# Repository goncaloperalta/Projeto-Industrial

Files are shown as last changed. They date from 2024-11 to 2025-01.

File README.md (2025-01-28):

# Automatic, universal push-button actuator, equipped with force gauge
## Table of contents
- [Overview](#overview)
- [Requirements](#requirements)
- [Pre-installation](#pre-installation)
- [Installation](#installation)
- [Interacting with the system](#interacting-with-the-system)

## Overview
This repository contains all the code to run the system, the PCB's files and the 3D designs.

## Requirements
This software is expected to run on a Raspberry Pi 4B (or equivalent), running **Raspberry Pi OS** not needing the graphical interface. 

## Pre-installation
Before installing, you must configure the way you want to connect to the Raspberry.
You can either connect it to the local network or use it has an access point.
> The former option is worse since you may run into conflits if the gateway ip of the local network and the ip of the DUT are the same.

To enable the access point run the command:

	sudo nmcli device wifi hotspot ssid <network-name> password <password>

If you want to disable it:

	sudo nmcli device disconnect wlan0
	sudo nmcli device up wlan0

The ethernet port must also be configured to have a static IPv4 (something like `192.168.1.5`), the gateway IP must be `192.168.1.1` and the route should not be set as default. That can be done using the `nmtui` command:

	sudo nmtui

You **must** also create a file inside the [control-code](control-code/) folder called `credentials.py`. The contents of the file should be the credentials used to connect to the DUT via SSH, formatted as:

	host="<hostname of the DUT>"
	pass="<password>"

without the characters `<` and `>`. 
## Installation
Start by installing `docker` and `docker-compose` with:

	sudo apt install docker.io docker-compose

then add your user to docker:

	sudo gpasswd -a $USER docker
	newgrp docker

finally clone the repository, `cd` into it and run a container with:

	docker compose up -d --build

Since this is the first time, it may take some minutes to finish building. After that you should see on port `:3000` the home page of the interface running, meaning the system is ready.

## Interacting with the system
The main way to interact with the system is to use the web interface on port `:3000`, however you can also use the a RESTful API on port `:8000`. On the **API Reference** page of the web interface you can see all the endpoints, what the returns are and a sample code to use it, you can also view the [api-reference.pdf](documents/api-reference.pdf) file which contains the same content.

The API is independent of the web interface and can be run without it but the opposite is not possible.

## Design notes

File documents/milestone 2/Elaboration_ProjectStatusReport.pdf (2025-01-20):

## 42088 – Industrial Project

# Project Status Report

## Milestone 2 – Elaboration

Project name: | Automatic, universal push-button actuator, equipped with force gauge
Customer: | Altice Labs
Customer supervisor: | Eng. Hélder Alves Eng. Nuno Balseiro
Date issued: | 06/11/2024
Team members: | Coordinator: Cláudia Almeida, claudiasalmeida@ua.pt, 914102617. Other team members: Rafael Alves, rafael01@ua.pt , 937353627. Gonçalo Peralta, goncaloperalta@ua.pt , 916828627. Pedro Matias, pedrodsmatias@ua.pt , 917126548.
Supervisor: | Professor Pedro Fonseca
Class supervisor: | Professor Pedro Fonseca

## Management summary:

The project is on track to meet its delivery deadlines. The team has successfully finished the Inception phase and is now actively working on the Elaboration phase. The component list, hardware circuit designs, and use case definitions are all now being finalized. There have been no substantial delays, and all the important components are being scheduled for purchasing within the current timeframe. As a consequence of the most recent meetings with the customer and the project supervisor, where the more technical issues were discussed, the electronic components were picked to ensure the product's flawless operation, resulting in an adjustment to the final budget. As we move into the Construction phase, the integration of the actuator, force sensor, and API, with iterative testing will be closely monitored, intended to address any compatibility issues early on.

## Architecture

The architecture of the system consists of three main components: the Control Unit, the Control Electric Circuit, and the Mechanical Actuation.

- The Control unit is managed by a Raspberry Pi that runs the control software and serves as the central processing component for the system. The Raspberry Pi generates a PWM (Pulse

Width Modulation) signal to regulate the actuator’s movement, allowing for controlled button pressing with variable force. It also maintains a Secure Shell (SSH) connection with the DUT, allowing it to detect feedback from the device in real time, such as system responses or status changes upon a button click. For force measurement, the Raspberry Pi reads data from the force sensor using I2C/SPI protocols, ensuring accurate and timely data transfer from the sensor to the control software.

- The Control electric circuit amplifies the PWM signal generated by the Raspberry Pi, ensuring sufficient power is supplied to the actuator. This circuit includes an H-Bridge, allowing current to flow in both directions as required to control the actuator’s movement accurately. The circuit, powered by a 12V, 3A DC power source, will provide the energy needed to drive the actuator with stability and precision, allowing for both pressing and releasing movements, required for testing various types of buttons.
- The Mechanical Actuation assembly is designed to interface directly with the DUT, positioning the actuator over the buttons to be tested. This component includes a clamp that securely attaches to the DUT, providing flexibility and adaptability for different button placements and device sizes. Mounted within the clamp is a linear actuator that performs the physical pressing of the buttons, with a force sensor placed behind the actuator to capture the exact force applied during each press. This assembly connects to a PCB board, which relays signals from the force sensor back to the Control Unit, ensuring accurate control and data capture throughout the testing process.

Figure 1 shows the improved and updated mechanical design of the product.

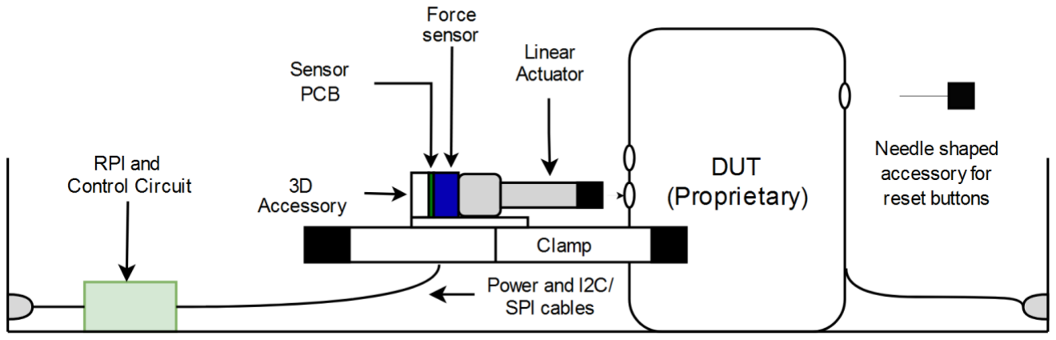
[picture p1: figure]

Figure 1. Mechanical assembly of the product.

Figure 2 shows the Unified Modelling Language (UML) Sequence Diagram, which represents the interaction amongst the different components of the system.

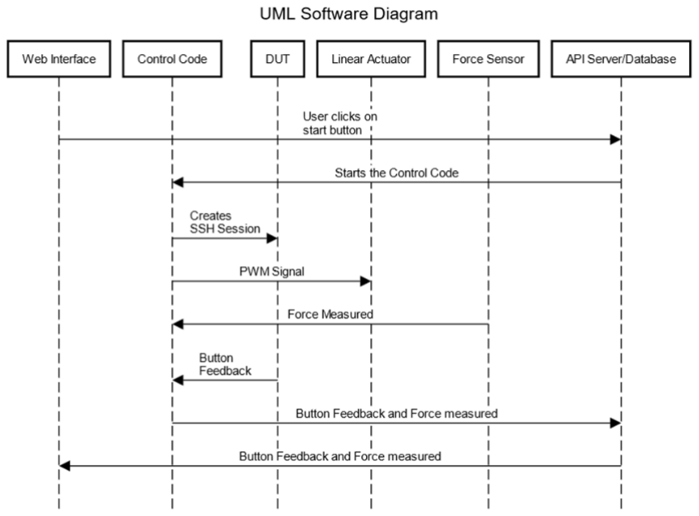
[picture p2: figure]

Figure 2. UML Diagram.

## Key milestones

ID | Description | Original planned completion date | Current planned completion date | Actual completion date
Project Vision | Market and needs to which the project responds | 23/10/2024 | --- | 23/10/2024
Project Plan | Working Phases, Budget and Risk List | 23/10/2024 | --- | 23/10/2024
Mock Up | A physical model of the system | 23/10/2024 | --- | 23/10/2024
Hardware | Final Component Lists | 30/10/2024 | 5/11/2024 | 6/11/2024
Project Status Report – M2 Elaboration | A summary of the current project status | 6/11/2024 | 6/11/2024 | 6/11/2024

Project Use
Cases – M2
Elaboration

Description of user interaction with
the product | 6/11/2024 | 6/11/2024 | 6/11/2024
Software Web Interface | Suggested visual presentation of the web interface | 13/11/2024 | 13/11/2024
Hardware PCB’s design | Design of the system's printed circuits and electrical circuits | 13/11/2024 | 20/11/2024

## Progress and deviation from plan

The project has generally progressed well; however, finalizing and structuring the component list took an additional seven days beyond the original timeline. This delay has impacted the timeline for requesting and purchasing the components, which may cause slight setbacks in the hardware assembly phase. To overcome this impediment of progress on the hardware testing side, we're going to move forward with the printed circuit boards, which are a fundamental part of starting tests, and start working and simulating data reception on the Raspberry Pi's web interface.

## Work plan for next iteration

In the next iteration, our primary focus will be on the design of the hardware printed circuit boards (PCBs) to support the control electric circuit for the actuator and force sensor. As the team anticipates some waiting time for component deliveries, we plan to adjust our schedule by beginning web page development for the Raspberry Pi ahead of schedule and design some visual presentation of the Web interface itself in various stage of its use. This will allow us to lay the foundation for the control interface, enabling future integration with the actuator and force sensor. Table 2 shows the sprint plan updated.

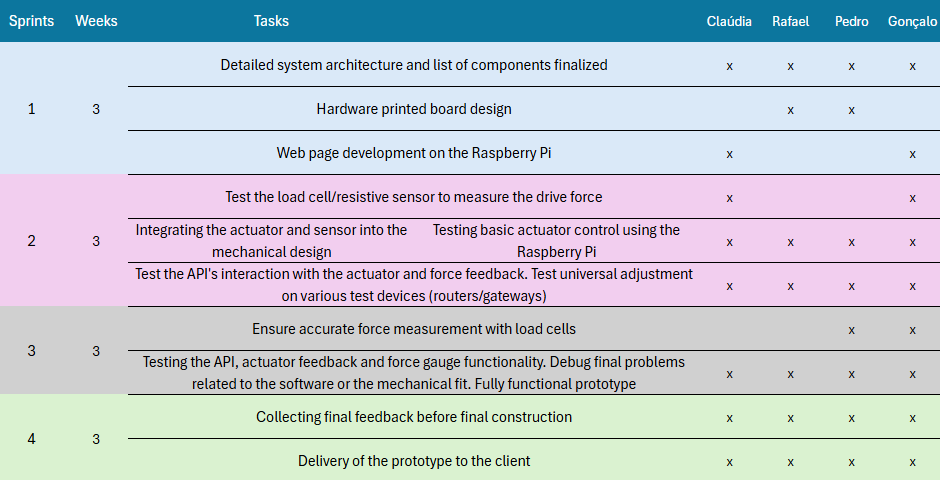
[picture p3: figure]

Table 2. Work sprints plan and schedule.

## Financial status

Following the development of the system's architecture in the previous iteration report, the team undertook a more in-depth investigation of the components needed to achieve the project specifications. This extensive analysis proved that our initial component selections were generally correct. However, it resulted in a significant rise in the overall budget.
One of the main factors contributing to this rise is the necessity for components with operating ranges and characteristics that better match our project's requirements, which are much more expensive. For instance, we wanted to replace the linear actuator to a type with a lower maximum force to ensure compatibility with our system, but this model costs roughly triple the amount. Similarly, we chose a more precise force sensor because force measurement is crucial for our product. This sensor, while more expensive, will significantly improve the accuracy and reliability of test results.
The remaining increase in the overall cost is due to small and inexpensive components that we did not include in the previous presented budget.

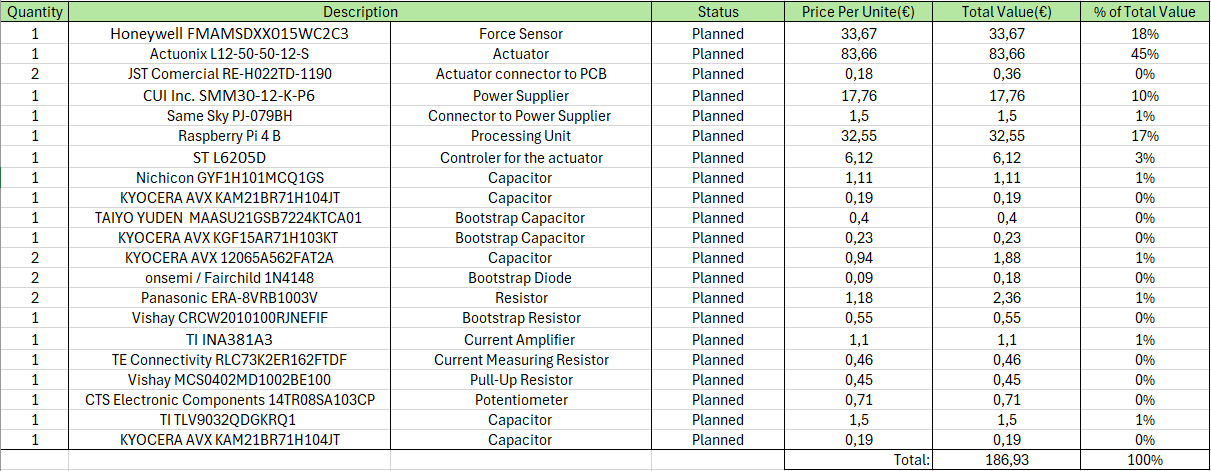
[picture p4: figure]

## Group contribution

Group member | Major contributions | Work share (%)
Cláudia Almeida | Team coordinator, responsible for organizing regrouping sessions and managing communication with external parties. Primary editor of written documents, developed the use cases, studied market relevance for industrial automation, and led Milestone 1 presentation. | 25
Rafael Alves | Developed the final hardware components list, analysed project risks for each phase and proposed mitigation strategies, and led Milestone 1 presentation. | 25
Gonçalo Peralta | Created all system diagrams and drafts of the mechanical product for documentation, developed the block diagrams and use cases, sprints spread calendar and led the initial planning for the software approach to the project. | 25
Pedro Matias | Contributed to researching and finalizing the hardware components list and supported the assessment of technical needs for project phases. | 25

## Comments and remarks

Attached are the documents relating to the risk analysis of the project and the block diagrams of the system broken down into various levels.

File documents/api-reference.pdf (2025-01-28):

# API Reference

This web interface runs on port :3000 , however the system also provides a RESTful API on port :8000 . Anything done in this web interface is based on this API.
The API accepts and returns only JSON encoded objects with no need for authentication. There are diferent ways to use it, one is with Python :

import requests
url = 'http://<ip>:8000/<Endpoint>'
headers = {
"Content-type": "application/json" }

res = requests.get(url, headers=headers)
print(res.text)

In each of the endpoints bellow it's provided the expected returns and a sample code to use it. All code can be seen on the GitHub (https://github.com/goncaloperalta/Projeto-Industrial) repository.

STATUS

GET | /api | ⮝

Returns a message if the API is up and running.

{
"message": "API running."
}

Sample python code:

import requests

url = "http://localhost:8000/api" headers = {
"Content-type": "application/json" }
res = requests.get(url, headers=headers)
print(res.text)
GET | /get-status | ⮝

Returns a message with the current state which can be on of the following:

{
// Ready to start a test
"message": "Ready"
// Already running a test
"message": "Running a test" // Aborting the running test "message": "Aborting the test" }

Sample python code:

import requests

url = "http://localhost:8000/get-status" headers = {
"Content-type": "application/json" }
res = requests.get(url, headers=headers)
print(res.text)
GET | /get-current-parameters | ⮝

If a test is running, returns an object with the parameters being used:

{ // If a test is running
"pressTime": 0
"pressTime": 1
"pressTime": 0
}
{ // If no test is running "message": "Not running a test" }

Sample python code:

import requests

url = "http://localhost:8000/get-current-parameters" headers = {
"Content-type": "application/json"
}
res = requests.get(url, headers=headers)
print(res.text)
GET | /get-logs | ⮝

Returns a file with the logs of the last test done. Can be accessed by just opening on the browser.

RUN A TEST

POST | /start | ⮝

Starts a button test, with the given parameters or profile chosen. If a valid profile is given the other parameters are ignored. A request with no body starts the test with parameter nTimes equal to one an the others set to zero. Returns one of the following messages:

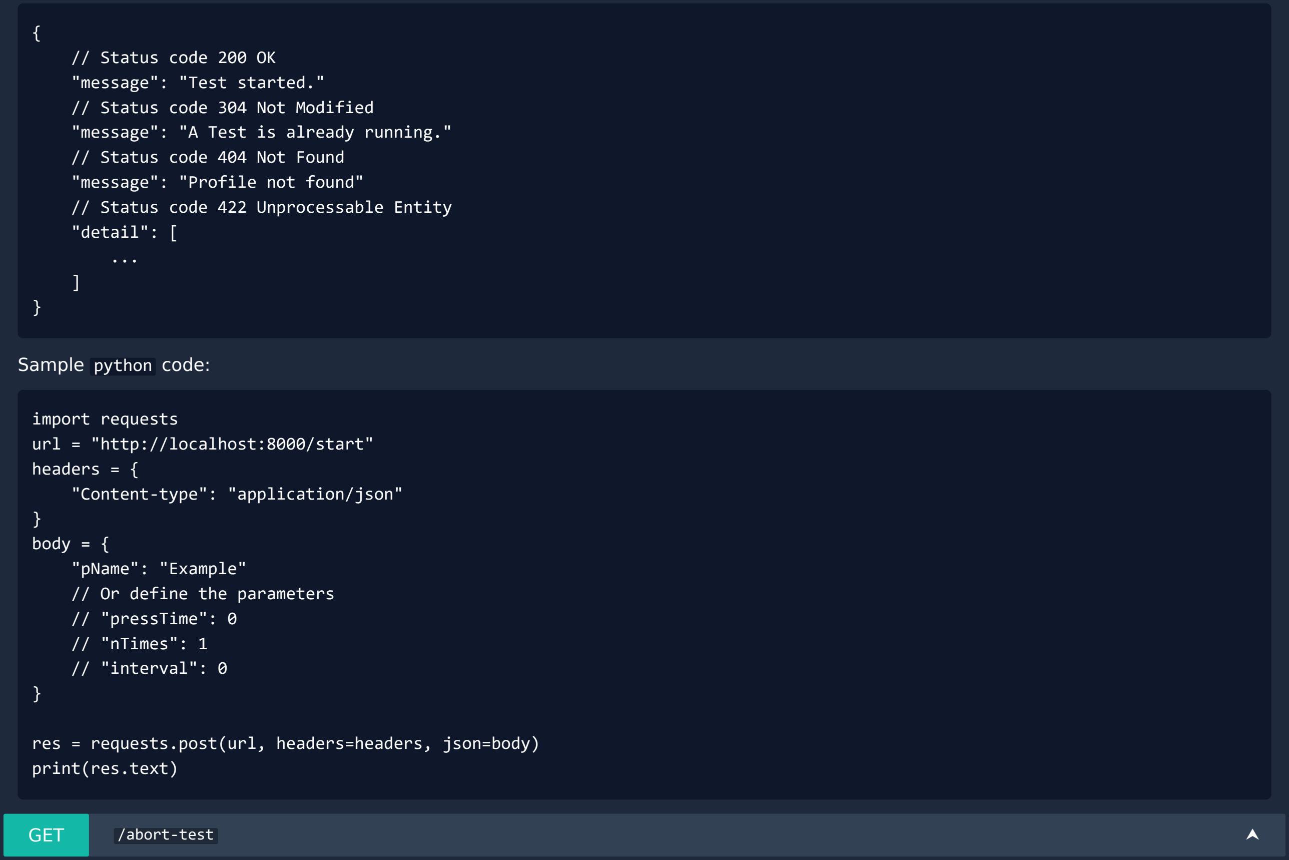
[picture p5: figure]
// Status code 200 OK "message": "Test started." // Status code 304 Not Modified "message": "A Test is already running." // Status code 404 Not Found "message": "Profile not found" // Status code 422 Unprocessable Entity "detail": [ ...; Sample python code:; import requests url = "http://localhost:8000/start" headers = { "Content-type": "application/json"; } body = { "pName": "Example" // Or define the parameters // "pressTime": 0 // "nTimes": 1 // "interval": 0; res = requests.post(url, headers=headers, json=body) print(res.text); GET; /abort-test

If a test is running aborts it. The test will only abort after finishing the current actuation

{
"message": "No test to abort" "message": "Test Aborted"
}

Sample python code:

import requests

url = "http://localhost:8000/abort-test" headers = {
"Content-type": "application/json" }
res = requests.get(url, headers=headers) print(res.text)

TESTS DATA

GET | /get-test-data | ⮝

Returns a file a JSON file with the all tests done from newest to oldest. Using a browser you can open the link directly and a download should appear. Data has the format:

[
{
"id": 5,
"button": "WPS",
"success": 1,
"error": "No error",
"presses": 2,
"parameters": "[0, 2, 1]",
"force_val": "[[1, 2, 3, 4, 5], [1, 2, 3, 4, 5]]", "time_val": "[[1, 2, 3, 4, 5], [1, 2, 3, 4, 5]]", "date": "2024-12-30",
"time": "11:45:43"
},
]
GET | /get-tests | ⮝

Returns all tests done, from newest to oldest, with format:

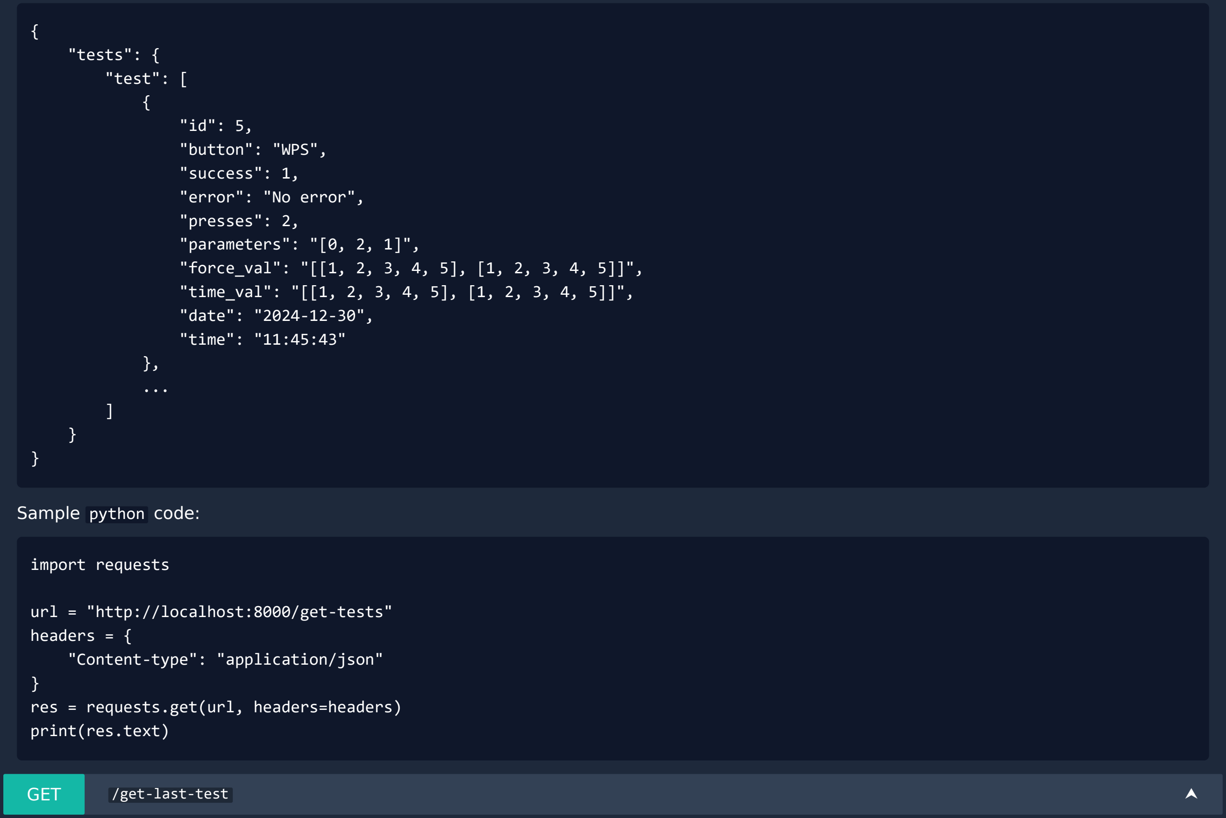
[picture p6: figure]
"tests": { "test": [ {; "id": 5, "button": "WPS", "success": 1, "error": "No error", "presses": 2, "parameters": "[0, 2, 1]",; "date": "2024-12-30", "time": "11:45:43"; Sample python code:; import requests; url = "http://localhost:8000/get-tests" headers = { "Content-type": "application/json"; } res = requests.get(url, headers=headers) print(res.text); GET; /get-last-test

"force_val": "[[1, 2, 3, 4, 5], [1, 2, 3, 4, 5]]", "time_val": "[[1, 2, 3, 4, 5], [1, 2, 3, 4, 5]]",

Returns only the last test done:

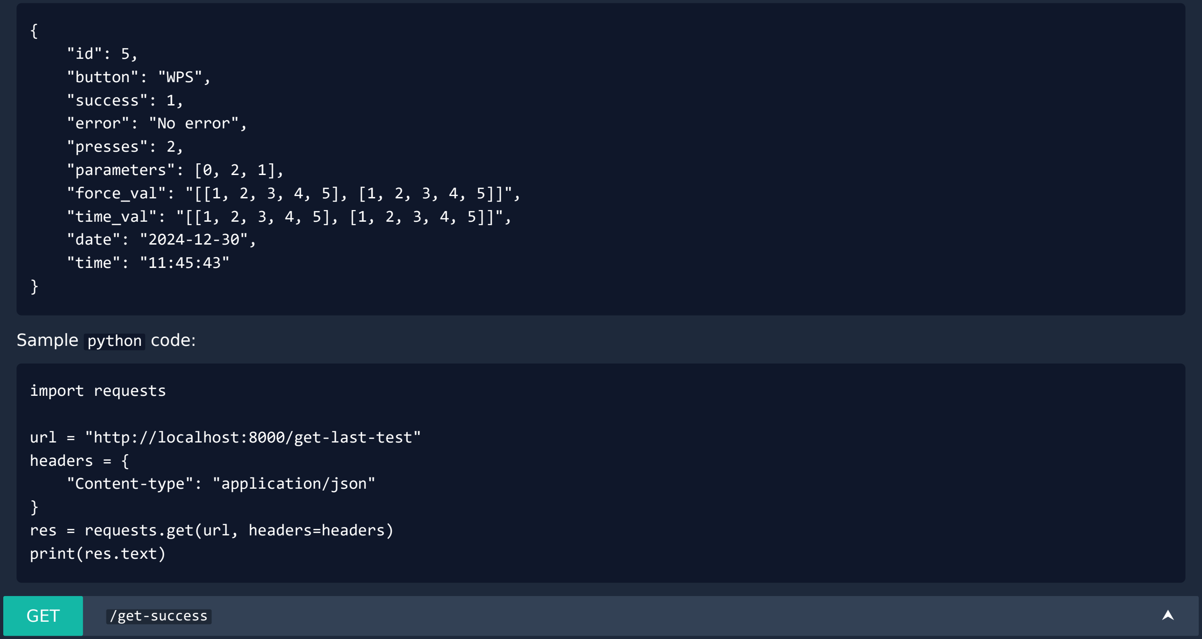
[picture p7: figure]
"id": 5, "button": "WPS", "success": 1, "error": "No error", "presses": 2, "parameters": [0, 2, 1],; "date": "2024-12-30", "time": "11:45:43"; Sample python code:; import requests; url = "http://localhost:8000/get-last-test" headers = { "Content-type": "application/json"; } res = requests.get(url, headers=headers) print(res.text); GET; /get-success

"force_val": "[[1, 2, 3, 4, 5], [1, 2, 3, 4, 5]]", "time_val": "[[1, 2, 3, 4, 5], [1, 2, 3, 4, 5]]",

Returns the success of all tests done:

[
1,
1,
0,
]

Sample python code:

import requests

url = "http://localhost:8000/get-success" headers = {
"Content-type": "application/json"
}
res = requests.get(url, headers=headers)
print(res.text)
POST | /get-tests-range | ⮝

Returns a defined range of tests:

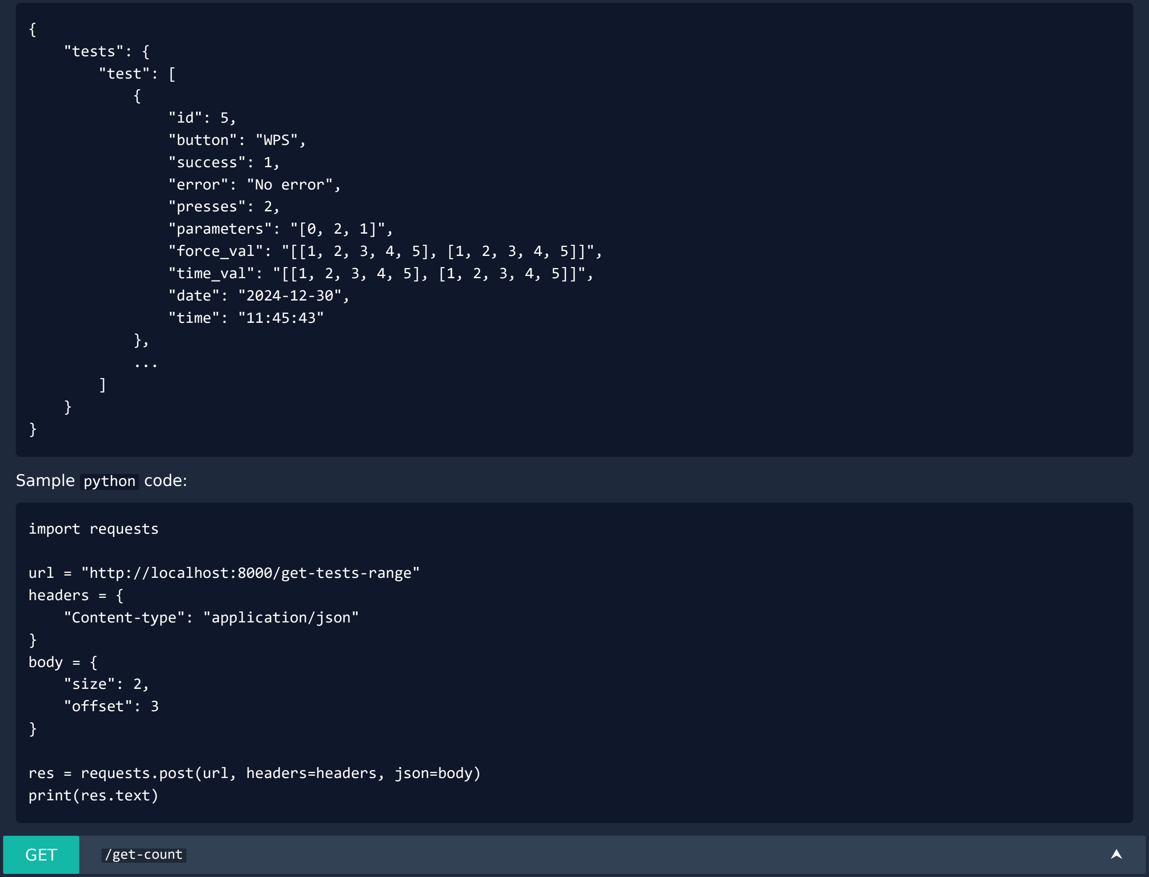
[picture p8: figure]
"tests": { "test": [ {; "id": 5, "button": "WPS", "success": 1, "error": "No error", "presses": 2, "parameters": "[0, 2, 1]",; "date": "2024-12-30", "time": "11:45:43"; Sample python code:; import requests; url = "http://localhost:8000/get-tests-range" headers = { "Content-type": "application/json"; } body = { "size": 2, "offset": 3; res = requests.post(url, headers=headers, json=body) print(res.text); GET; /get-count

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

Returns the total number of tests done:

{
"count": 19
}

Sample python code:

import requests

url = "http://localhost:8000/get-count" headers = {
"Content-type": "application/json" }
res = requests.get(url, headers=headers)
print(res.text)
POST | /get-by-id | ⮝

Returns the test data with the same id:

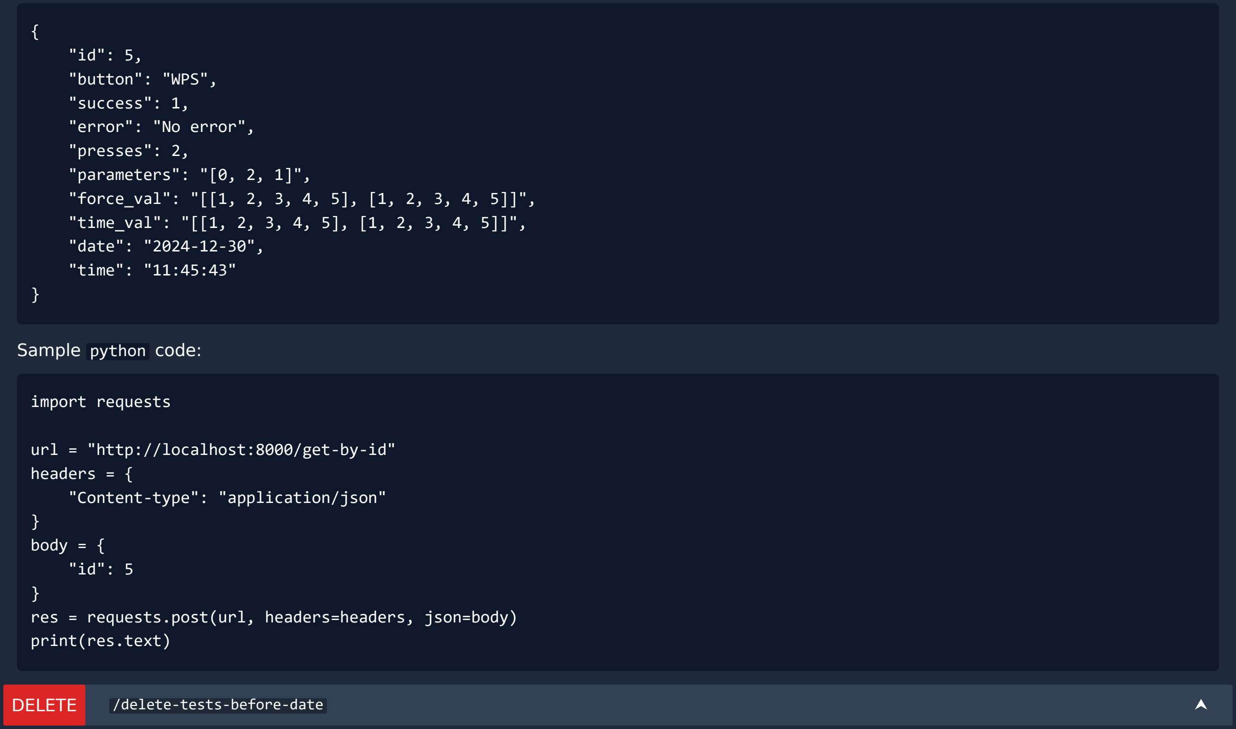
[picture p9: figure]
"id": 5, "button": "WPS", "success": 1, "error": "No error", "presses": 2, "parameters": "[0, 2, 1]",; "date": "2024-12-30", "time": "11:45:43"; Sample python code:; import requests; url = "http://localhost:8000/get-by-id" headers = { "Content-type": "application/json"; } body = { "id": 5; } res = requests.post(url, headers=headers, json=body) print(res.text); DELETE; /delete-tests-before-date

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

Deletes all tests before the given date:

{
"message": "Tests deleted" }

Sample python code:

import requests

url = "http://localhost:8000/delete-tests-before-date" headers = {
"Content-type": "application/json"
}
body = {
"day": "2024-12-30"
}
res = requests.delete(url, headers=headers, json=body) print(res.text)

PROFILES

GET | /get-profiles | ⮝

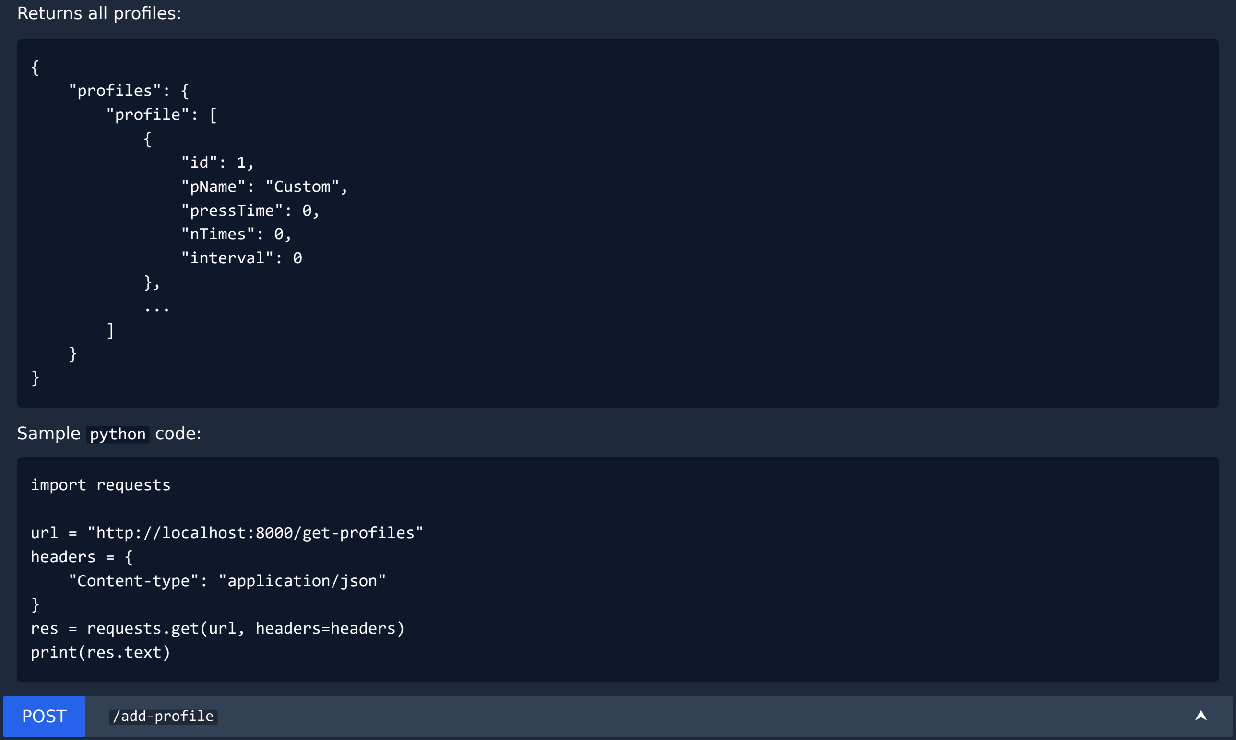
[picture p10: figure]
Returns all profiles:; "profiles": { "profile": [ {; "id": 1, "pName": "Custom", "pressTime": 0, "nTimes": 0, "interval": 0; Sample python code:; import requests; url = "http://localhost:8000/get-profiles" headers = { "Content-type": "application/json"; } res = requests.get(url, headers=headers) print(res.text); POST; /add-profile

Add a new profile with given parameters and name. Returns one of the messages:

{
"message": "Profile added to database." | // Status code 201 Created
"message": "A profile with that name already exists." | // Status code 400 Bad Request
}

Sample python code:

import requests

url = "http://localhost:8000/add-profile" headers = {
"Content-type": "application/json"
}
body = {
"pName": "Test Profile",
"pressTime": 3,
"nTimes": 2,
"interval": 1
}

res = requests.post(url, headers=headers, json=body)
print(res.text)
DELETE | /delete-profile | ⮝

Deletes a profile given it's name. Returns on of the messages:

{
"message": "Profile deleted from database." | // Status code 200 OK
"message": "Profile name not found." | // Status code 404 Not Found
}

Sample python code:

import requests

url = "http://localhost:8000/delete-profile" headers = {
"Content-type": "application/json"
}
body = {
"pName": "Test Profile"
}

res = requests.delete(url, headers=headers, json=body) print(res.text)

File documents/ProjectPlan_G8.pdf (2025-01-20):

## 42088 – Industrial Project

# Project Plan

Project name: | Automatic, universal push-button actuator, equipped with force gauge
Customer: | Altice Labs
Team members: | Coordinator: Cláudia Almeida, claudiasalmeida@ua.pt, 914102617. Other team members: Gonçalo Peralta, goncaloperalta@ua.pt , 916828627. Pedro Matias, pedrodsmatias@ua.pt , 917126548.

Rafael Alves, rafael01@ua.pt , 937353627.

Date: | 22/10/2024

Revision History
Date | Issue | Description | Author
22/10/2024 | Development Costs | Task phasing | Eng. Hélder Alves

## Objectives

The purpose of this project is to create a remotely controllable automaton that is capable of pressing buttons, validate their operation, measure the force required to activate them and communicate the results to the server. The solution must ensure that it interacts with various types of buttons (from soft-touch buttons to hard mechanical ones) safely and reliably, while collecting detailed data on the force applied and the button's response.
To achieve the intended end-result, an estimate of the required work was sub-divided into phases. This allows for efficient use of the group’s efforts to deliver an end-product with good characteristics and within the defined time frame.
Therefore, this report´s primary goal isto give a thorough assessment of how the work will be divided, how the project management will be done, the resources available for its development and the risks involved.

## Phase plan

Table 1. Work plan and schedule.

## 1.1 Objectives of each iteration

As seen in table 1, the project’s life cycle was divided into 4 major phases that in turn are divided into iterations. These divisions were pre-defined by the course with basis on an OpenUP framework, with a presentation on the end of each (and in the middle of the “Construction”) phase to show all progress achieved.

Inception
This report is written in the end of the Inception phase, and its main objective was to ensure that the entire group had a clear understanding of the proposed work, and the steps required to successfully complete it. More specifically, it was necessary to understand the purpose of the product and the needs
Week | Date
1 | 18/09/2024
2 | 25/09/2024

3

Meeting and Brainstorm with the Company

Team approval of project
requirements and initial design concepts
| 17/10/2024
4 | 23/10/2024
5 | 30/10/2024
6 | 11/06/2024
7 | 13/11/2024
8 | 20/11/2024

9

Integrating the actuator and sensor into
the mechanical design

Testing basic actuator control using the Raspberry Pi

| 27/11/2024
10 | 12/04/2024
12 | 25/12/2024
13 | 01/01/2025

15
16
17 | 17/1/2025

Web page development on the Raspberry Pi

Construction

Test the load cell/resistive sensor to measure the drive force

Transition

Delivery of the prototype to the client

Test the API's interaction with the actuator and force feedback. Test universal adjustment on various test devices (routers/gateways)

Ensure accurate force measurement with load cells

Inception

Detailed system architecture and list of components finalized

Hardware printed board design

Task
Understand the problem, determine initial requirements and submit proposals with solutions

Definition of the concept to be developed in the project

Elaboration

11 | 12/11/2024

Collecting final feedback before final construction

Testing the API, actuator feedback and force gauge functionality. Debug final
problems related to the software or the mechanical fit. Fully functional prototype

01/08/2025 of the devices under test (DUT), in order to create a timeline, a project and team management plan, and to develop a list of necessary components along with the corresponding budget, as well as a list of potential associated risks, ensuring an appropriate response to the problem presented.

Elaboration
In this phase the main objective is to define the system architecture and to transform the high-level vision developed during the Inception Phase into a practical and concrete plan for building the system. This means the system’s architecture will be clearly defined, including its structure, components and how they interrelate. This architecture will serve as the blueprint for development, providing a detailed plan of how the system will be built, operated and maintained. This phase focuses on organising the various parts of the system (e.g., actuator, force sensor, Raspberry Pi, API and software interface) in a way that illustrates how they will interact. By defining these interrelationships early, the team can ensure that all components work together seamlessly, and potential integration issues are addressed upfront. Here, proof of concepts and prototypes will play a significant role in mitigating risks. By testing core components (such as the actuator's control and the force sensor’s accuracy), potential issues can be identified early, and solutions can be refined before full-scale construction begins.
We will also take a deeper plunge into drawing up the necessary technical specifications for each component. This includes selecting the most suitable technologies (e.g. linear actuators, resistive force sensors), outlining the printed circuit board (PCB), defining the data flow and specifying the signal conditioning circuits and other essential infrastructures.
Since the goal is to take the general vision from Inception and break it down into detailed, actionable plans, technical diagrams, flowcharts, and interface definitions will be created to explain "how" the system will be implemented—whether it’s the physical setup of the actuator, the software architecture for the API, or the integration of the force sensor and data transmission protocols.

Construction
The goal of this phase is to start building the product that was designed in the earlier stages. Having the components required in hand, work force is focused on constructing the modules and testing them. The effort required to complete this task is likely high, and as such requires parallelism, minimizing stalls and delivery times.

For this, the development is split into two concurrent development trees, the API and the hardware. Both start with lower-level component development and testing to guarantee a solid foundation - for example the force sensor, and the base operating system for the Raspberry Pi - and rise to the model expected – e.g. proper motor control and working API.
The evolution of each tree will not be done top-down simply in one version, but rather it will be done in iterations that allow the communication between the API and the mechanical interface to be achieved as quickly as possible so to increment functionality. Afterwards, they will be fully tested in conjunction to achieve a working product.

Transition
In this phase, the final product will be delivered and presented, and so it should be a fully functioning product to be tested by users. From there feedback will be used to improve the experience and ensure it works as intended. We will conduct an evaluation of the satisfaction level from our side, as well as from the company and the professors.

## 2 Budget

This is a raw estimate of the cost associated with this product, but it will be more accurately updated in the elaboration phase.

ID | Category | Description | Value (€)
1 | Components | Linear Actuator https://mauser.pt/catalog/product_info.php?products_id=0 95-0732 (https://mauser.pt/catalog/product_info.php?products_id=095-0732) | 32.65
2 | Components | Raspberry Pi https://mauser.pt/catalog/product_info.php?products_id=0 95-3807 (https://mauser.pt/catalog/product_info.php?products_id=095-3807) | 19.99
3 | Components | Force-Sensing Resistor https://mauser.pt/catalog/product_info.php?products_id=0 96-6326 (https://mauser.pt/catalog/product_info.php?products_id=096-6326) | 14.70
4 | Components | 8 bit Analog-to-Digital Converter https://mauser.pt/catalog/product_info.php?products_id=0 01-2384 (https://mauser.pt/catalog/product_info.php?products_id=001-2384) | 5.92
Total: | 73.26
Table 2. Components and respective costs.
ID | Category | Description | Value (€)
1 | Development | Perforated circuit board https://mauser.pt/catalog/product_info.php?products_id=096-4828 | 5.24
Total: | 5.24
Table 3. Development costs.

Altice Labs offered us the opportunity to use their 3D printer and materials, as well as supply the PCB that will be designed, allowing us to focus on development without concerns about those costs. However, it will always be kept in mind that the lower the implementation cost, the easier it will be to replicate the final product.

## 3 Resources

Our team consists of four students from Electronics and Telecommunications Engineering course, supported by one supervisor from the Department of Electronics, Telecommunications, and Informatics (DETI), and two engineers from Altice Labs.
To maximize each member's abilities and to guarantee that everyone is actively involved in the various phases of the project, the group will be split up into pairs or, in certain cases, some members will work alone. It is also important to mention that the group has a project coordinator, who is primarily responsible for managing the team and serves as the liaison between the group and the different supervisors.

We will implement the Scrum project management methodology using the software Trello, (https://trello.com/) with sprints lasting three weeks, shown in Table 2, along with daily short meetings and a more extended weekly meeting with the project supervisor for planning and evaluating the work done. At the end of each sprint, we will have a demo product, where we will discuss for improvements to prepare the next sprint.

Table 2. Work sprints plan and schedule.

It is worth mentioning that even though sometimes in these sprints plan not all the members are included in a task, this means they will be working in other tasks, not specified, that must be done continually during the semester, like the development of the fixture piece and report’s/presentation preparation.

## 4 Risks and Constrains

Product Risks:

- Linear actuator pushing the buttons too hard, damaging the equipment;
Solution: defining a fixed maximum value of pressure, by limiting the output of the amplifier.
- Poor placement of the automaton on the DUT, creating a misalignment between the actuator and the buttons;
Solution: use a flexible clamp to ease the placement according to the button position.
- Improper placement of the force-sensitive resistor, causing the applied force to not be measured correctly;
Solution: ensure the FSR placement gives an accurate measurement on the given test devices, by testing different locations for its application.

Project Risks:

- PCB taking up to two or three weeks to build, and it may end up not working; Solution: Use a perforated circuit board instead which will take just a few days to set up.
- Delay on the delivery of the components, slowing the overall progress of the project; Solution: Approach the problem with temporary equipment.
- Poor team and time management, which can lead to task accumulation;
Solution: Follow the Scrum methodology, helping us to overcome this problem.
Sprints Weeks | Claúdia Rafael | Pedro Gonçalo
x | x | x | x
| x | x
x | | | x
| | | x
Integrating the actuator and sensor into the mechanical design

Testing basic actuator control using the Raspberry Pi

x | x | x | x
x | x | x | x
| | x | x
x | x | x | x
x | x | x | x
x | x | x | x

2

3

4

Tasks

3

3

3

3

Test the load cell/resistive sensor to measure the drive force

Test the API's interaction with the actuator and force feedback. Test universal adjustment on various test devices (routers/gateways)
Ensure accurate force measurement with load cells Testing the API, actuator feedback and force gauge functionality. Debug final problems related to the software or the mechanical fit. Fully functional prototype

Web page development on the Raspberry Pi

Collecting final feedback before final construction

Detailed system architecture and list of components finalized

1 | Hardware printed board design

Delivery of the prototype to the client

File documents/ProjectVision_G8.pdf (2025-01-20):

## 42088 – Industrial Project

# Project Vision

Project name: | Automatic, universal push-button actuator, equipped with force gauge
Customer: | Altice Labs
Team members: | Coordinator: Cláudia Almeida, claudiasalmeida@ua.pt, 914102617. Other team members: Rafael Alves, rafael01@ua.pt, 937353627. Gonçalo Peralta, goncaloperalta@ua.pt, 916828627. Pedro Matias, pedrodsmatias@ua.pt, 917126548.
Date: | 23/10/2024

Revision History
Date | Issue | Description | Author
22/10/2024 | Manual button testing approach | Exploring the problem, outlining a solution, assessing possible risks | Eng. Hélder Alves

## 1 Project description

The goal of this project is to automate the process of pressing buttons, checking their operation, and determining the force required to activate them. Traditionally, button testing has been done manually, which requires the presence of a person at the test site, making remote actuation of the buttons by the automatic tests unfeasible. Additionally, manual actuation can make it difficult to perceive when the button clicks and when it does not, especially when there are many buttons to press in sequence. Pressure force appears as another variable that is difficult to measure accurately by humans, as pass/fail criteria will be subjective from person to person. Automating this operation improves precision, reproducibility, and dependability, particularly in circumstances where many buttons of various sorts and sizes must be examined. Our proposed solution fits the needs of Altice Labs and opens the door to broader industrial applications by being universally adaptable to varied devices under test (DUT). This project addresses the growing demand for automation in testing processes across sectors. This automated technology has major advantages, including increased testing speed, greater data accuracy, and the ability to remotely control and monitor the testing process. As a result, it will improve the workflow for firms like Altice Labs, which test network gateways, routers, and other devices with physical interfaces lowering labour costs, enhancing product reliability and test more software releases in less time.
The system guarantees that force is applied consistently, yielding precise and reproducible findings, which is critical for determining if devices satisfy the required requirements. Furthermore, it is intended to accommodate a wide number of devices by adapting to different button sizes and mechanisms, making it applicable to a diverse range of products. The capacity to collect detailed force measurements and process information will also allow businesses to make data-driven decisions that will advise design changes, increase product reliability, and direct manufacturing adjustments.

## 2 Deliverables/Outcome

The tangible deliverables will feature a fully functional prototype of the automated button actuator system, controlled via an API and capable of pressing various types of buttons with adjustable force. This system will incorporate a linear actuator for precise movement, a resistive force sensor for measuring applied force, and custom-designed accessories (potentially 3D-printed) to ensure compatibility with different devices. Additionally, a complete software solution will be developed to remotely manage the actuator and collect data, transmitting test results to a server for analysis. Figure 1 shows a practical sketch of the automaton to be built.

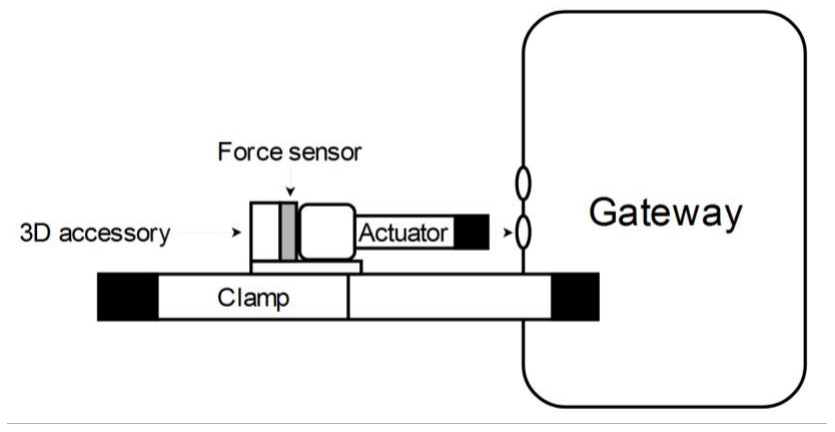
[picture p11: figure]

Figure 1. Global design of the automaton.

On the intangible side, the project will generate valuable technical expertise gained in designing and building automated testing systems, integrating actuators and sensors with microcomputers like the

Raspberry Pi as well as knowledge of force measurement techniques and how to apply them in realworld testing environments.

## 3 Functionality and Technology

The system will automate the task of pressing buttons on various devices, such as network gateways and routers, while measuring the force required to activate each button. The interaction between users, primarily the test engineers at Altice Labs, and the final product will be largely remote rather than physical. The system is designed to be easily applied to the DUT without the need for manual adjustments, such as fine-tuning the height or positioning relative to the buttons being tested. Instead, users will interact with the system through an intuitive web interface which will display all test history stored in the database. This interface will deliver the main advantage of the project: providing realtime statistics on the force applied during tests, as well as feedback on the functionality of the buttons by allowing to initiate button tests remotely from any connected device, adjust test parameters, including the amount of force to apply, and select the type of DUT.

To achieve the system's functionality, several key technologies will be used. A Raspberry Pi will act as the central controller, managing communication between the linear actuator, force sensor, and server. The linear actuator will perform the button pressing, offering precise movement and force control, making it adaptable to various button types. A resistive force sensor will measure the applied force during each press, with data converted by an Analog to Digital Converter (ADC) for processing by the Raspberry Pi, ensuring accurate force readings. The system will also feature an API and web interface to enable remote control and automation of tests, allowing users to adjust settings and retrieve data easily. Additionally, custom 3D-printed fixtures will be designed/adapted to hold the actuator and DUTs securely, ensuring a universal fit for a variety of devices.

The system will operate within the testing labs of Altice Labs, where test engineers can physically set up the DUTs. However, the remote capabilities of the system, enabled through the web interface and API, will allow users to control the testing process from any location connected to the lab network.

## 4 Customer / End users / Market

The primary target user of our project is the test engineering team at Altice Labs, who will directly use the automated button actuator system to test devices such as routers and gateways. These engineers are responsible for ensuring the functionality and reliability of these devices before they are released to the market. While they will operate the system, the stakeholders extend beyond just the test engineers. The product development team will benefit from the accurate and consistent testing data that can be used to improve product design, while the quality assurance (QA) team will rely on the system’s results to verify that devices meet required specifications before production.
In a further sense, Altice Labs' management team is also a stakeholder, as automation will increase efficiency, reduce testing time and potentially lower labour costs, aligning with the company's objectives of improving productivity and streamlining operations.

To measure customer satisfaction, several key factors can be considered once the product is in use:
- Efficiency gains: The improvement in software testing time during daily software releases, through the inclusion of button tests in current automatic software tests, thus increasing the automatic tests coverage, eliminating the need for manual tests on buttons.
- Accuracy: The precision and consistency of force measurements and button functionality results.
- Usability: Feedback from test engineers on the intuitiveness and user-friendliness of the system.

- Reliability: The system's ability to handle various types of devices consistently, without failures or frequent adjustments.

By assessing these factors, we can ensure that the system meets the needs of its direct users, while providing value to all the stakeholders involved in the project.

## 5 Partners

This project has a key institutional partner: Altice Labs, a leading technology company focused on innovation and development in telecommunications and IT solutions. Altice Labs plays a crucial role as both the client and collaborative partner in this project.
Its main role includes:
- Providing the problem statement: Altice Labs has defined the scope and objectives of the project, aiming to automate the testing of devices such as routers and gateways by developing an automated button actuator.
- Technical Support and Resources: Through offering access to their workspaces, equipment, and test devices such as the Raspberry Pi and DUTs (devices under test). This support allows us to carry out preliminary tests.
- Component Sourcing: Altice Labs will assist with the acquisition of necessary components, ensuring that there are no delays in delivery, thus helping us stay on schedule.
- Ongoing Feedback: Throughout the project, engineers from Altice Labs, such as Eng. Hélder and Eng. Nuno, are actively involved in providing technical feedback and guidance. They will help validate key design decisions and ensure that the final product meets their operational requirements.

In addition to the company that proposed the challenge, we are fortunate to have the guidance and support of Professor Pedro Fonseca, from the Department of Electronics and Telecommunications at the University of Aveiro. He will be closely involved throughout the entire project, providing mentorship and oversight from the initial planning stages through to the final proof of concept.

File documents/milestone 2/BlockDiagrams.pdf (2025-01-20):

## 42088 – Industrial Project

# Block Diagrams

## Milestone 2 – Elaboration

Project name: | Automatic, universal push-button actuator, equipped with force gauge
Customer: | Altice Labs
Customer supervisor: | Eng. Hélder Alves Eng. Nuno Balseiro
Date issued: | 06/11/2024
Team members: | Coordinator: Cláudia Almeida, claudiasalmeida@ua.pt, 914102617. Other team members: Rafael Alves, rafael01@ua.pt , 937353627. Gonçalo Peralta, goncaloperalta@ua.pt , 916828627. Pedro Matias, pedrodsmatias@ua.pt , 917126548.
Supervisor: | Professor Pedro Fonseca
Class supervisor: | Professor Pedro Fonseca

## Table of Contents

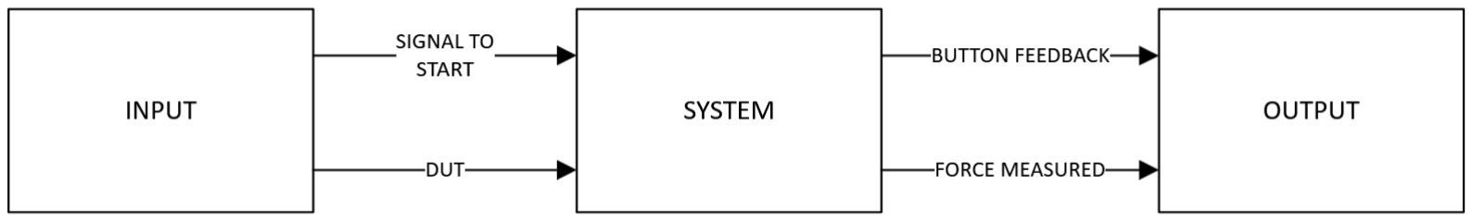
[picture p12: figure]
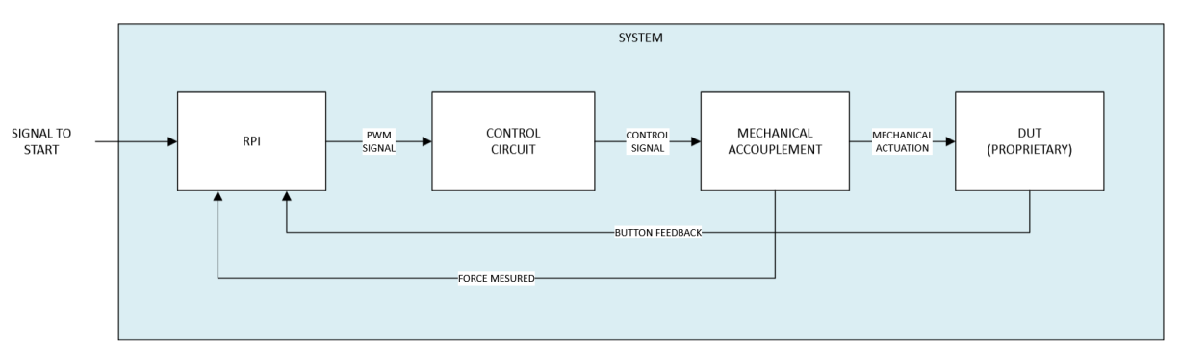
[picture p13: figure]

DETI – Industrial Project | Altice Labs

## 1. Introduction

This document presents all the block diagrams in our project divided by levels, each one proving more detailed information on the architecture of the corresponding system.

## 2. Level 0 Diagram

Figure 1. Level 0 Diagram.

The Level 0 diagram of the system represents the simplest view of its functionality. At this level, the system receives two main inputs: a command to start the test and a device under test (DUT) with a specific button to be evaluated. The system then performs the test by pressing the button, and the outputs generated include feedback on the button’s operation status and the precise force applied during the press. This high-level view captures the essential workflow, where the system translates a test command into actionable data on button functionality and force measurement.

## 3. Level 1 Diagram

Figure 2. Level 1 Diagram.

The Level 2 diagram of the system provides a closer look at its core components, which are organized into three main blocks:

1. Raspberry Pi: Acting as the control unit, the Raspberry Pi serves as the primary interface between the user and the system. It processes user commands, initiates the test sequence, and communicates with the actuator and force sensor, capturing feedback on button functionality and force data.
2. Control Circuit: This circuit is responsible for amplifying the signals output from the Raspberry Pi to match the power requirements of the actuator. It ensures that the actuator receives adequate power and current direction for precise button pressing without straining the Raspberry Pi’s limited GPIO output.
3. Mechanical Actuation: This component consists of the actuator and force sensor. The actuator is responsible for physically pressing the button on the DUT, while the force sensor captures the exact force applied during each press. Together, they enable accurate and repeatable testing of button functionality.

Each of these blocks is detailed further in subsequent levels, where specific functions, components, and interactions within each part of the system are described.

## 4. Level 2 Diagrams

## 4.1 RPI

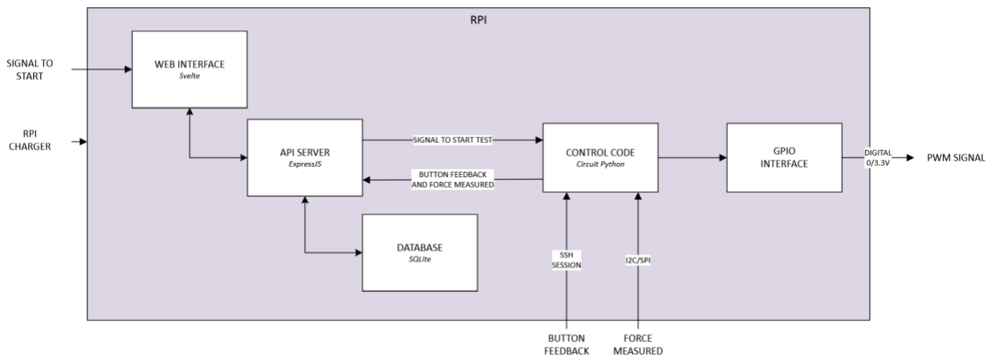
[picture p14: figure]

Figure 3. Diagram Level 2 - Raspberry Pi.

In the Level 2 diagram focused on the Raspberry Pi, the system is organized around two primary components: the web server and the control code.

1. Web Server: This component provides the main user interface for configuring and initiating tests. Through the web server, users can interact with the system via a web page accessible from any device within the same network. The web server hosts a database to store test readings, enabling users to access and analyze historical data.

Additionally, it runs an API server that facilitates communication between the web interface, database, and the control code, ensuring seamless data flow and command execution.
2. Control Code: This component manages the Raspberry Pi’s GPIO interface to control the testing process. It sends a PWM signal to the control circuit to drive the actuator for button pressing. The control code also establishes an SSH session with the DUT, allowing it to read button feedback directly from the device. Additionally, it uses I2C or SPI protocols to communicate with the force sensor, capturing precise force measurements during the test. All readings from the DUT and force sensor are then sent back to the API, making them accessible to the web server for real-time monitoring and record-keeping.

Together, these components allow the Raspberry Pi to control, monitor, and document the testing process, providing a complete interface for remote, automated button testing.

## 4.2 Control Circuit

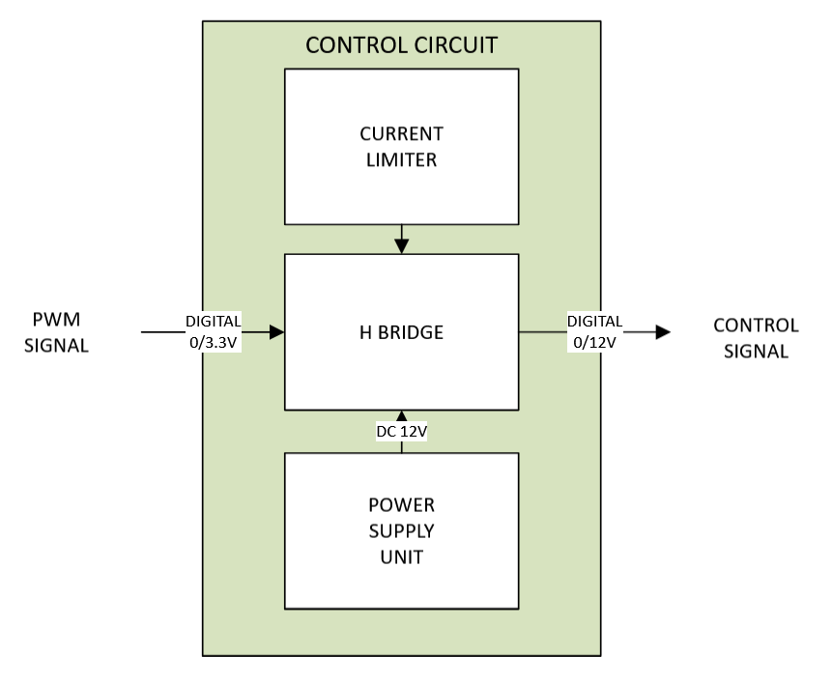
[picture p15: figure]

Figure 4. Diagram Level 2 - Control Circuit.

In the Level 2 diagram focused on the Control Circuit, the circuit’s main purpose is to amplify the output from the Raspberry Pi’s GPIO interface to provide sufficient power for the actuator, which the Raspberry Pi alone cannot support.

1. Signal Amplification: The Raspberry Pi’s GPIO output is too low to directly drive the actuator, so the control circuit amplifies the signal to the necessary power level.

2. H-Bridge Configuration: Unlike a standard NOT gate, which only allows current flow in a single direction, the control circuit uses an H-Bridge configuration. This setup enables bi-directional current flow, which allows the actuator to both push forward and retract, supporting complete actuation control.
3. Power Supply: The entire circuit is powered by a 12V 3A DC power supply. This supply provides the necessary voltage and current for the actuator to operate smoothly, ensuring stable power delivery throughout the testing process.

Together, these components effectively amplify the PWM signal from the Raspberry Pi and provide controlled, bi-directional movement of the actuator, enabling precise button testing operations.

## 4.3 Mechanical Accouplement

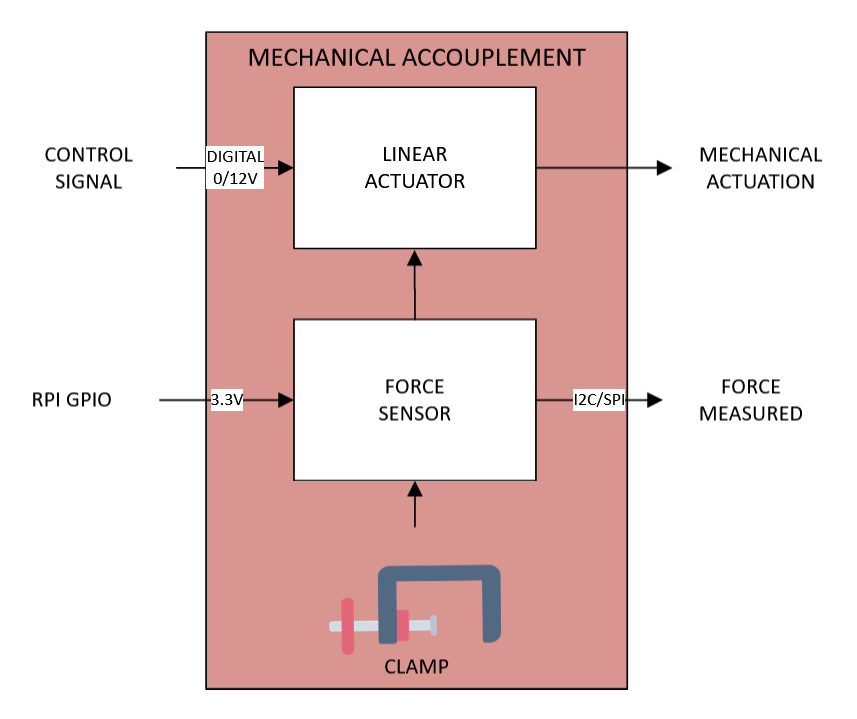
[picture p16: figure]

Figure 5. Diagram Level 2 - Mechanical Accouplement.

A clamp secures the force sensor and linear actuator in precise alignment, ensuring that the actuator can press the DUT’s button accurately. This design allows for stable positioning and adaptability across various DUTs, keeping the components securely in place during testing.

The force sensor is powered by the Raspberry Pi’s GPIO interface, which provides sufficient power for sensor operation. Communication with the force sensor occurs via SPI or I2C protocols to accurately capture force data. The Raspberry Pi's built-in ADC (Analog-to-

Digital Converter) processes these readings, allowing for real-time data capture of the force applied.

The linear actuator is controlled by the amplified PWM signal provided by the control circuit. This amplified signal enables the actuator to apply the required force to press the button, ensuring precise and controlled actuation that matches the DUT’s requirements.

## 4.4 DUT

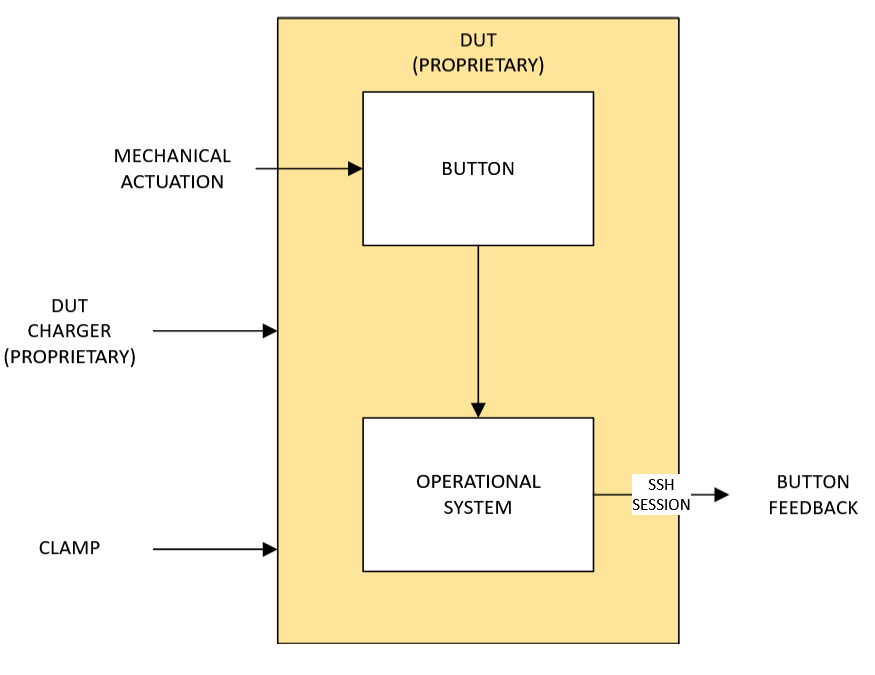
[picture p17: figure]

Figure 6. Diagram Level 2 - DUT (Proprietary).

The DUT is a proprietary device, such as a gateway, and is not directly part of our system. However, our system interacts with the DUT in two primary ways to ensure effective testing:

1. Physical Interaction: The DUT is securely attached to the clamp within the system. This setup allows the linear actuator to press the DUT’s button accurately, ensuring consistent and repeatable tests.
2. Feedback Monitoring: During testing, the Raspberry Pi initiates an SSH session with the DUT’s operating system, enabling it to monitor real-time feedback. This feedback helps verify button functionality, such as confirming successful button presses or identifying any issues. For this interaction to occur, the DUT must be powered on.

This block illustrates the interface between our system and the DUT, highlighting both the physical alignment for button pressing and the digital connection for monitoring responses.

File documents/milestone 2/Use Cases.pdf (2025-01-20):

## 42088 – Industrial Project

# Use Cases

## Milestone 2 – Elaboration

Project name: | Automatic, universal push-button actuator, equipped with force gauge
Customer: | Altice Labs
Customer supervisor: | Eng. Hélder Alves Eng. Nuno Balseiro
Date issued: | 06/11/2024
Team members: | Coordinator: Cláudia Almeida, claudiasalmeida@ua.pt, 914102617. Other team members: Rafael Alves, rafael01@ua.pt , 937353627. Gonçalo Peralta, goncaloperalta@ua.pt , 916828627. Pedro Matias, pedrodsmatias@ua.pt , 917126548.
Supervisor: | Professor Pedro Fonseca
Class supervisor: | Professor Pedro Fonseca

## Introduction

This paper describes the software requirements and use cases for the automated button actuator system, which is intended to evaluate the functionality of various buttons on devices under test (DUTs). The system's objective is to automate button testing by delivering precise force to each button and assuring consistent, repeatable interactions. The system will be operated by an API and a web interface, allowing for remote control and data collecting. It will also generate useful testing data such as force exerted and device reaction.
The Software Requirements Specification (SRS) specifies the software components of the automated button actuator system. It describes how the system will communicate with DUTs using remote commands, capture force data, validate button answers, and provide a user-friendly interface for test engineers. This document will also describe the use scenarios for the DUT's three buttons (Reset, WPS, and Info) and the intended results for each.

## Purpose

This article serves as an in-depth guide for Altice Labs test engineers on how to operate the Automated Button Actuator with Force Measurement system. The setup, operation, and button testing of the actuator system are covered in this article, along with steps for starting tests, tracking force data, and reading test outcomes. It is meant to guarantee that end users can efficiently use the features of the system to perform reliable, accurate, and efficient button testing across a range of devices.

## Scope

The Automated Button Actuator with Force Measurement system's functionality is fully described in this document. It contains thorough use cases and functional requirements that together provide a thorough manual for use the system for testing applications. It includes everything Altice Labs test engineers need to know to set up, start, and keep an eye on button testing using the actuator system. Instructions for remote control, data collecting, and result interpretation are included to guarantee precise, reliable testing on a variety of devices.

## System Overview

The purpose of this project is to automate button testing, which includes pressing buttons, checking their operation, and determining the force required to activate them. Traditional manual testing can be inconsistent and time-consuming, making remote and exact testing difficult, particularly for devices with numerous buttons. Automating this procedure improves precision, consistency, and dependability, allowing Altice Labs to test buttons remotely and more accurately across a variety of DUTs. This technology increases testing speed, data accuracy, and workflow efficiency, benefiting applications other than Altice Labs by cutting labour costs and enabling data-driven advances in product design, reliability, and manufacturing. The system will be adjustable to various button kinds and sizes, making it a versatile, scalable solution that matches the demands of modern testing environments.

## References

Previously drafted documents that can provide a good insight into the project:

- Project Vision Document: Contains the overall vision, purpose, customer market and high-level objectives of the Automated Button Actuator project.
- Project Plan Document: Outlines the project’s management, timeline, resources available and risks involved.

## Definitions

API (Application Programming Interface): An API is a set of rules and protocols that enable various software components to communicate and interact with one another. In this project, the API acts as a link between the user interface and the automated button actuator system, allowing remote control and monitoring of the testing process. Test engineers can use the API to start tests, change parameters (such as force settings), and receive data from the system, all from a connected device. This allows for seamless engagement with the actuator system without requiring direct, physical operation, making testing more efficient and accessible.

DUT: Device under test.

## Use Cases

Name | UC-1: Test Definition
Summary | Definition of the characteristics of the test that will be performed.
Rationale | DUT’s come with various types of buttons with different sizes, stiffness and functionalities that alter based on the time it is pressed. Keeping in mind that many aspects are unique to each test; in order to obtain reliable results, the user must set the parameters that best fit the test he wishes to run.
Users | Test Engineers
Preconditions | The webpage is open, in a default state and ready to be configured.
Basic Course of Events | 1. The user should specify: a. What button will be tested; b. How long the actuator should hold the button down (short press or long press); c. Number of times to be pressed; d. Maximum force that can be applied to the button; e. Interval between actuations.
Alternative Paths | 1. In step 1, if the user does not input any data, the system will proceed to use default values instead. 2. In step 1. d, if the user enters an imposed force value that is close to or exceeds the value set as the maximum acceptable value or an out-of-range value, the system will display a warning message and suggest acceptable ranges.

Postconditions | Test is now defined, and the user can click on the start button on the Web interface to initiate it.
Name | UC-2: Test Realization
Summary | Realization of the test.
Rationale | Manual button testing has always been an inefficient, repeating time-consuming task for Test Engineers. This Use-Case immediately follows the previous UC-1.
Users | Test Engineers
Preconditions | The webpage already contains information on the test characteristics.
Basic Course of Events | 1. The test engineer holds the clamp on the DUT in an adequate position to push the button; 2. The test engineer must ensure that the DUT is powered on and ready to respond to button presses 3. On the webpage, the test engineer clicks on the start button; 4. The test engineer waits while the automaton pushes the button; 5. Once the operation is over, graphics and results regarding applied force over time are shown on the webpage for user information.
Alternative Paths | 1. In step 1, to test a reset button, the user should additionally add the needle shaped accessory; 2. In step 4, if the clamp isn’t positioned appropriately it may lead to the button not be pushed correctly or not pushed at all. The user should abort the test using the web interface and repeat from step 1.
Postconditions | The test has ended, and the results are available on the website.
Name | UC-3: Accessing older tests and statistics
Summary | Viewing older tests and overall statistics
Rationale | Statistics are important to extract meaningful patterns to maximize corporate profits.
Users | Company management teams
Preconditions | Webpage is open.
Basic Course of Events | 1. The user accesses the Statistics tab in the Web interface; 2. The page responds by plotting the overall tests done and a search bar; 3. The user filters the parameter through which they would like to access past tests.
Alternative Paths | 1. In step 2 if there’s a failure in retrieving data due to a system error or loss of connection and the system displays the message “Unable to retrieve test data. Please check your connection or try again later.” the user can retry the action, refresh the page; 2. In step 2 if only part of the data loads (e.g., due to server latency or heavy data volume) the system will display a loading indicator and will prompt the user with the message: "Loading data, please wait."

| If loading times out, the user will be given the option to retry or narrow the search parameters. 3. In step 3 in case the system displays the message “No results found matching the selected parameters.”, the user can modify the filter criteria or clear the filters to view all available tests;
Postconditions | A table is shown with the tests performed on that period/parameter.

## Functional Requirements

Name | FR-1: Data input webpage
Summary | Platform that allows the users to configure and start the test.
Rationale | This web page is what allows the user to customize the test he wants to perform to the best fit and start it.
Requirements | • User must be able to input the test configuration data; • System should validate the inputted data and only then allow to click on the start button.
References | UC-1: Test Definition
Name | FR-2: Results webpage
Summary | Platform that allows the users to see the result of the performed test.
Rationale | This web page is what allows the user to see the outputs of the system.
Requirements | System should show: • Basic data about the gateway (model, memory capacity, CPU…); • If the pressed button is functional; • Plot of the force over the time.
References | UC-2: Test Realization
Name | FR-3: Statistics webpage
Summary | Platform that allows the users to see the result of previous performed tests.
Rationale | This web page is what allows the user to see statistics of all tests made over the time.
Requirements | System should show a list of the more recent tests for easier accessibility; System should allow the user to search for specific tests based on: • A time period; • A specific type of button; System should also show plots of the number of tests over time and the overall button functionality.
References | UC-3: Accessing older tests and statistics
Name | FR-4: Compatibility of the DUT with the clamp
Summary | Verify DUT dimensions and button alignment before testing.
Rationale | The user must ensure before starting the test that the DUT meets the dimensions allowed and for which the product was developed, otherwise, it

| won't have the stability or precision to press buttons, and the purpose of the product won't be fulfilled.
Requirements | The test operator must first inspect the device in hand, in particular its design and should pay attention to conditions like: • The width of the device must not exceed the maximum opening of the claw, so that it can be attached to the device; • The DUT's surface must be smooth and stable enough for the clamp to attach securely. • The buttons on the device must be perpendicular to the surface of the device so that the user can position the clamp intuitively and directly to start the test.
References | UC-2: Test Realization
Name | FR-5: Automaton to press the buttons
Summary | Equipment that attaches to the DUT, allowing the actuator to push the buttons
Rationale | This is the equipment that allows the realization of automated and remote testing.
Requirements | System should do: • Receive the configurations introduced in the webpage; • Perform the pressing of buttons accordingly the test definition;
References | UC-2: Test Realization
Name | FR-6: Sensor to measure the applied force
Summary | Sensor that measures the necessary force to push the buttons and transmits that data to the website.
Rationale | This is the system that allows the users to study the forces applied in the buttons.
Requirements | The system should do: • Sensor measures the force applied; • Sensor measures for how long the force is applied; • Send that information to the website.
References | UC-2: Test Realization

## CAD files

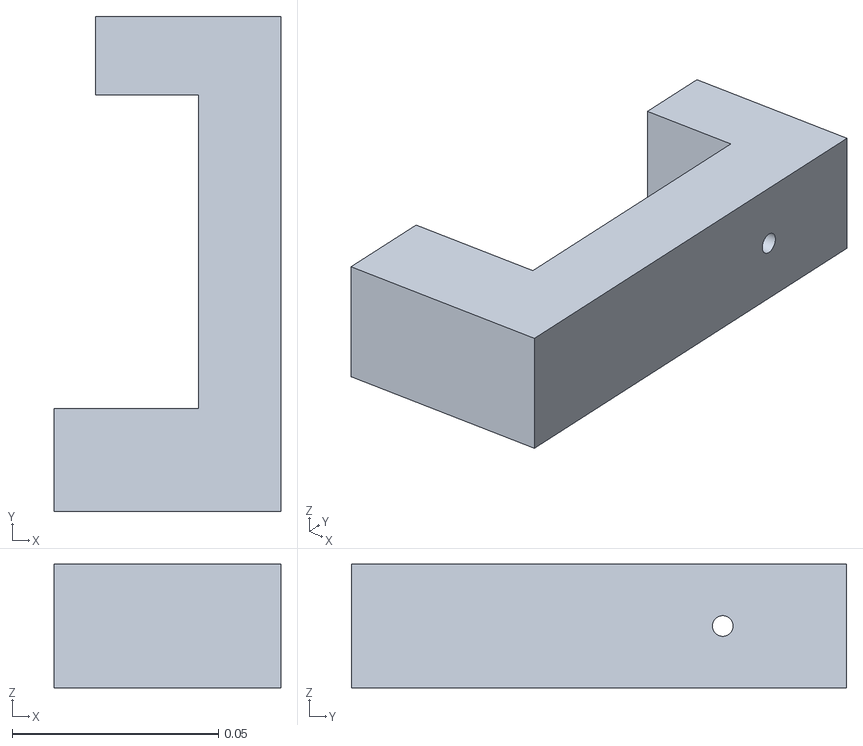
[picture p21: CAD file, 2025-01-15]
3d-designs/grampofinal.stl
0.055 x 0.12 x 0.03

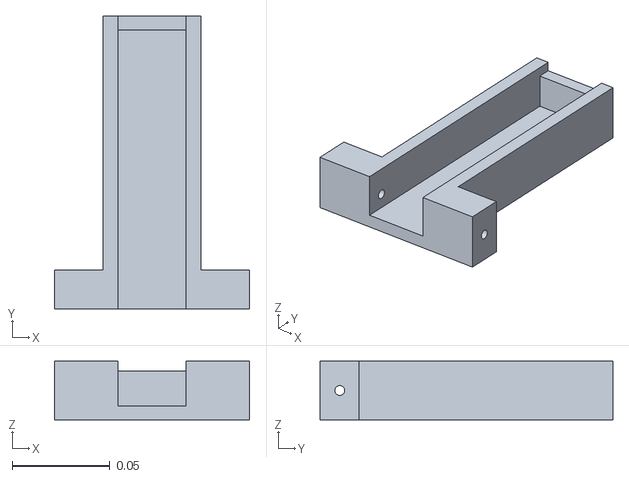
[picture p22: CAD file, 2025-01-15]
3d-designs/PeçaPrincipal.stl
0.1 x 0.15 x 0.03

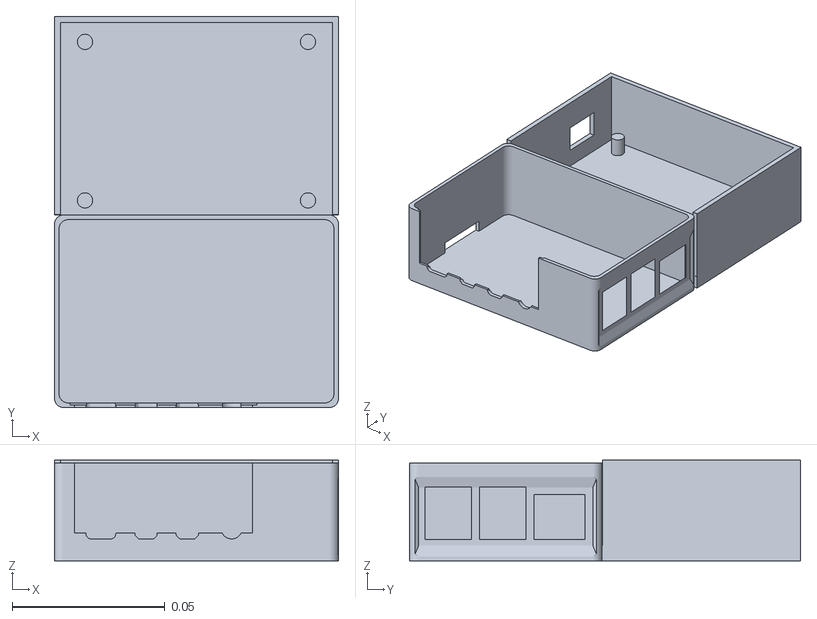
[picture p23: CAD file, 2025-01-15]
3d-designs/box.stl
0.093 x 0.128 x 0.033

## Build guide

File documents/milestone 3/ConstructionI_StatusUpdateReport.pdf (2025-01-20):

## 42088 – Industrial Project

# Project Status Report

## Milestone 3 – Construction I

Project name: | Automatic, universal push-button actuator, equipped with force gauge
Customer: | Altice Labs
Customer supervisor: | Eng. Hélder Alves Eng. Nuno Balseiro
Date issued: | 27/11/2024
Team members: | Coordinator: Cláudia Almeida, claudiasalmeida@ua.pt, 914102617. Other team members: Rafael Alves, rafael01@ua.pt , 937353627. Gonçalo Peralta, goncaloperalta@ua.pt , 916828627. Pedro Matias, pedrodsmatias@ua.pt , 917126548.
Supervisor: | Professor Pedro Fonseca
Class supervisor: | Professor Pedro Fonseca

## Management summary:

The project is on track to meet its delivery deadlines. The team has successfully completed the elaboration phase and is now transitioning into the construction phase of the project. At this stage, all of the necessary hardware components have been delivered. The PCBs required to power and control the actuator have been thoroughly designed and reviewed multiple times with guidance and feedback from both class and customer supervisor. Additionally, the first draft of the user interface was presented using simulated data to demonstrate functionality. Feedback was collected during this phase, and improvements are being incorporated to refine the interface for its next iteration.

As we move forward, our focus will shift to establishing communication with the Raspberry Pi, generating test data, processing feedback signals from the test gateway and start individual tests on main components such as the actuator and the force sensor. Meanwhile, we await the printing of the PCBs, after which we will proceed with assembling and soldering all the components. This marks an exciting and critical step in bringing the system closer to full functionality.

Considering all the progress and development to date, as well as the organization of future tasks, the team anticipates that all proposed objectives will be successfully achieved.

## Architecture

The architecture of the system consists of three main components: the Control Unit, the Control Electric Circuit, and the Mechanical Actuation.

- The Control unit is managed by a Raspberry Pi that runs the control software and serves as the central processing component for the system. The Raspberry Pi generates a PWM (Pulse Width Modulation) signal to regulate the actuator’s movement, allowing for controlled button pressing with variable force. It also maintains a Secure Shell (SSH) connection with the DUT, allowing it to detect feedback from the device in real time, such as system responses or status changes upon a button click. For force measurement, the Raspberry Pi reads data from the force sensor using I2C/SPI protocols, ensuring accurate and timely data transfer from the sensor to the control software.
- The Control electric circuit amplifies the PWM signal generated by the Raspberry Pi, ensuring sufficient power is supplied to the actuator. This circuit includes an H-Bridge, allowing current to flow in both directions as required to control the actuator’s movement accurately. The circuit, powered by a 12V, 3A DC power source, will provide the energy needed to drive the actuator with stability and precision, allowing for both pressing and releasing movements, required for testing various types of buttons.
- The Mechanical Actuation assembly is designed to interface directly with the DUT, positioning the actuator over the buttons to be tested. This component includes a clamp that securely attaches to the DUT, providing flexibility and adaptability for different button placements and device sizes. Mounted within the clamp is a linear actuator that performs the physical pressing of the buttons, with a force sensor placed behind the actuator to capture the exact force applied during each press. This assembly connects to a PCB board, which relays signals from the force sensor back to the Control Unit, ensuring accurate control and data capture throughout the testing process.

Figure 1 shows the improved and updated mechanical design of the product.

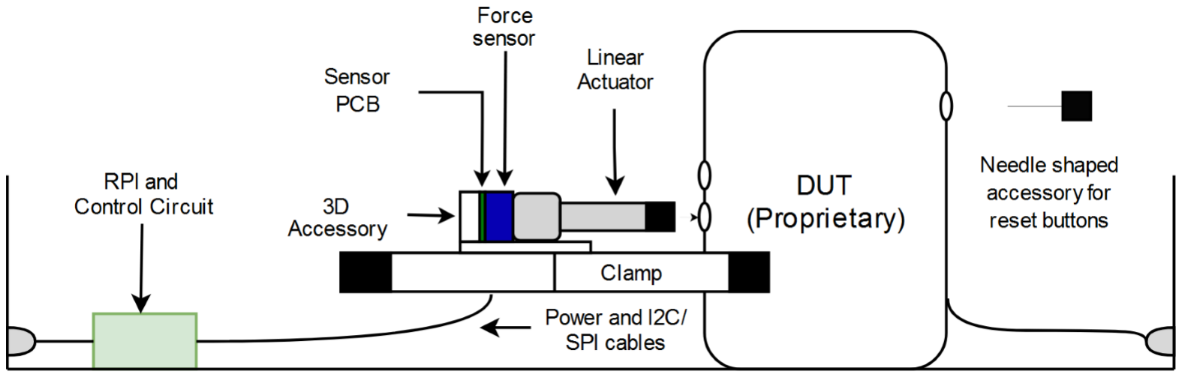
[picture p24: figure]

Figure 1. Mechanical assembly of the product.

Figure 2 shows the Unified Modelling Language (UML) Sequence Diagram, which represents the interaction amongst the different components of the system.

Figure 2. UML Diagram.

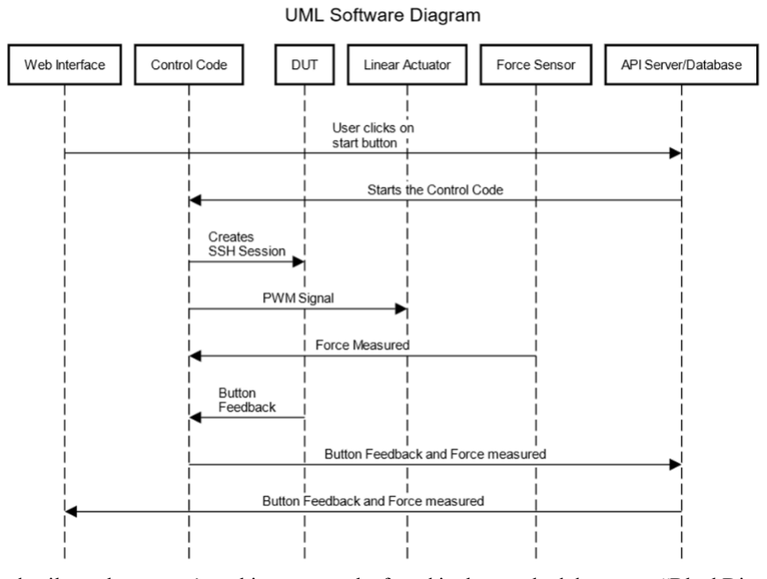
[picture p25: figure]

Further details on the system’s architecture can be found in the attached document “BlockDiagrams”.

## Key milestones

ID | Description | Original planned completion date
Current
planned
completion
date

Actual
completion
date
Software Web Interface | Suggested visual presentation of the web interface | 13/11/2024 | 13/11/2024 | 14/11/2024
Hardware PCB’s design | Design of the system's printed circuits and electrical circuits | 13/11/2024 | 18/11/2024 | 21/11/2024
Project Status | A summary of the current | 27/11/2024 | 27/11/2024 | 27/11/2024

Report – M3
Construction

project status

Communication
with Raspberry Pi

Generate test signals and
process feedback signals
from the DUT.
04/12/2024 | 04/12/2024 | 27/11/2024
Design of the mechanical attachment | Development of the mechanical couple using 3D print. | 04/12/2024 | 04/12/2024 | --/--/--
Individual tests to the main components | Functionality tests for the main components of the project: force sensor and linear actuator. | 04/12/2024 | 04/12/2024 | --/--/--

## Progress and deviation from plan

The development of the PCBs required extra effort to reach a level deemed suitable for the prototyping stage. This additional effort caused a small delay in finalizing the design, leading to a late printing order and, consequently, a significant portion of the testing will be delayed, temporarily stalling progress on the hardware side. To mitigate this deviation, the team will redirect their time to other tasks in two primary fronts: the first one being establishing communication with the Raspberry Pi, generating test data, and processing feedback signals from the test gateway, and the second one consisting on the designing of the mechanical attachment, to be developed using 3D printing.

## Work plan for next iteration

For the next iteration, individual tests on the actuator will be carried out. Additionally, the team will begin analysing and looking into the gateway's feedback signals through given credentials to access its operating system.

Table 2 shows the sprint plan updated.

Figure 3. Sprint plan

## Financial status

With respect to the project budget and components list, no modifications have been made since the previous milestone. Consequently, the order was placed as planned, and all required components have now been successfully delivered.

Figure 4. Updated project budget and final components table.

## Group contribution

Sprints Weeks | Claúdia Rafael | Pedro Gonçalo
x | x | x | x
Prototype a 3D support | Test basic Actuator control and SSH connection to the gateway with the RPi | x | x | x | x
Test the force sensor PCB | Test the controller PCB | x | x | x | x
| | x | x | x | x
x | x | x | x
x | x | x | x
x | x | x | x
4 | 2

Collecting final feedback before final construction

Delivery of the prototype to the client

Web page interface and all PCB's

3 3

Test the overall architecture

Develop a 3D model to support the architecture | Update the interface to match the control code
2 | 3

Merge everthing into a single control code

Detailed system architecture and list of components finalized

Tasks

PCB design for the control signal and the Force Sensor

Web page development and structurization of a control code on the Rpi

1 | 4
x | x | x | x
MVP's | We are currently here
x | x | x | x
Quantity | Description | Status | Price Per Unite(€) | Total Value(€) | %
1 | Honeywell FMAMSDXX015WC2C3 | Force Sensor | Purchased | 33,67 | 33,67 | 18% 45% 0% 10% 1% 17% 3% 1% 0% 0% 0% 1% 0% 1% 0% 1% 0% 0% 0% 1% 0%
1 | Actuonix L12-50-50-12-S | Actuator | Purchased | 83,66 | 83,66
2 | JST Comercial RE-H022TD-1190 | Actuator connector to PCB | Purchased | 0,18 | 0,36
1 | CUI Inc. SMM30-12-K-P6 | Power Supplier | Purchased | 17,76 | 17,76
1 | Same Sky PJ-079BH | Connector to Power Supplier | Purchased | 1,5 | 1,5
1 | Raspberry Pi 4 B | Processing Unit | Purchased | 32,55 | 32,55
1 | ST L6205D | Controler for the actuator | Purchased | 6,12 | 6,12
1 | Nichicon GYF1H101MCQ1GS | Capacitor | Purchased | 1,11 | 1,11
1 | KYOCERA AVX KAM21BR71H104JT | Capacitor | Purchased | 0,19 | 0,19
1 | TAIYO YUDEN MAASU21GSB7224KTCA01 | Bootstrap Capacitor | Purchased | 0,4 | 0,4
1 | KYOCERA AVX KGF15AR71H103KT | Bootstrap Capacitor | Purchased | 0,23 | 0,23
2 | KYOCERA AVX 12065A562FAT2A | Capacitor | Purchased | 0,94 | 1,88
2 | onsemi / Fairchild 1N4148 | Bootstrap Diode | Purchased | 0,09 | 0,18
2 | Panasonic ERA-8VRB1003V | Resistor | Purchased | 1,18 | 2,36
1 | Vishay CRCW2010100RJNEFIF | Bootstrap Resistor | Purchased | 0,55 | 0,55
1 | TI INA381A3 | Current Amplifier | Purchased | 1,1 | 1,1
1 | TE Connectivity RLC73K2ER162FTDF | Current Measuring Resistor | Purchased | 0,46 | 0,46
1 | Vishay MCS0402MD1002BE100 | Pull-Up Resistor | Purchased | 0,45 | 0,45
1 | CTS Electronic Components 14TR08SA103CP | Potentiometer | Purchased | 0,71 | 0,71
1 | TI TLV9032QDGKRQ1 | Capacitor | Purchased | 1,5 | 1,5
1 | KYOCERA AVX KAM21BR71H104JT | Capacitor | Purchased | 0,19 | 0,19
| | | | Total: | 186,93 | 100%

Group member | Major contributions | Work share (%)
Cláudia Almeida | Team coordinator, responsible for organizing regrouping sessions and managing communication with external parties. Primary editor of written documents, developed the use cases, studied market relevance for industrial automation, and led Milestone 1 presentation. Web interface Development. | 25
Rafael Alves | Developed the final hardware components list, analysed project risks for each phase and proposed mitigation strategies, and led Milestone 1 presentation. Development of the PCB. | 25
Gonçalo Peralta | Created all system diagrams and drafts of the mechanical product for documentation, developed the block diagrams and use cases, sprints spread calendar and led the initial planning for the software approach to the project. Web interface Development. | 25
Pedro Matias | Contributed to researching and finalizing the hardware components list and supported the assessment of technical needs for project phases. Development of the PCB. | 25

## Comments and remarks

Attached are the documents relating to the risk analysis of the project and the block diagrams of the system broken down into various levels.

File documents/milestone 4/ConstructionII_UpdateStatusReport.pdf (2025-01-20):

## 42088 – Industrial Project

# Project Status Report

## Milestone 4 – Construction II

Project name: | Automatic, universal push-button actuator, equipped with force gauge
Customer: | Altice Labs
Customer supervisor: | Eng. Hélder Alves Eng. Nuno Balseiro
Date issued: | 18/12/2024
Team members: | Coordinator: Cláudia Almeida, claudiasalmeida@ua.pt, 914102617. Other team members: Rafael Alves, rafael01@ua.pt , 937353627. Gonçalo Peralta, goncaloperalta@ua.pt , 916828627. Pedro Matias, pedrodsmatias@ua.pt , 917126548.
Supervisor: | Professor Pedro Fonseca
Class supervisor: | Professor Pedro Fonseca

## Management summary:

The project is on track to meet its delivery deadlines. The team has successfully completed the initial construction phase and is now transitioning into its final phase of the project where a minimum viable product is expected to be achieved. At this stage, the PCB board has been soldered and tested, showing correct operation. Both the linear actuator and the force sensor were tested individually. The actuator behaved correctly to the commands outlined in Python code by the Raspberry Pi, adjusting its excursion and speed of movement according to the current limitation imposed and the duty cycle programmed. The force sensor correctly measured manually applied forces and provided feedback. The mechanical claw has been printed and has matched the expected result. It is currently undergoing some manual changes and screw positioning to provide more stability for the components it will support. The most recent update includes an extra added support for the force sensor to add stability and be centred with the actuator, to correctly measure the force exerted.

As we move forward our focus will be on improving the overall coupling of all physical parts to a more elegant and discreet version and improve the web interface and data processing of the API in relation to the Raspberry Pi.

## Architecture

The architecture of the system consists of three main components: the Control Unit, the Control Electric Circuit, and the Mechanical Actuation.

- The Control unit is managed by a Raspberry Pi that runs the control software and serves as the central processing component for the system. The Raspberry Pi generates a PWM (Pulse Width Modulation) signal to regulate the actuator’s movement, allowing for controlled button pressing with variable force. It also maintains a Secure Shell (SSH) connection with the DUT, allowing it to detect feedback from the device in real time, such as system responses or status changes upon a button click. For force measurement, the Raspberry Pi reads data from the force sensor using I2C/SPI protocols, ensuring accurate and timely data transfer from the sensor to the control software.
- The Control electric circuit amplifies the PWM signal generated by the Raspberry Pi, ensuring sufficient power is supplied to the actuator. This circuit includes an H-Bridge, allowing current to flow in both directions as required to control the actuator’s movement accurately. The circuit, powered by a 12V, 3A DC power source, will provide the energy needed to drive the actuator with stability and precision, allowing for both pressing and releasing movements, required for testing various types of buttons.

Figure 1 presents PCB, assembled with the support of an Altice Labs engineer. A total of five PCBs were manufactured; one was fully soldered by the engineer to ensure high-quality assembly, while another was soldered by the team as a learning exercise to develop soldering skills. For testing and development, the PCB soldered by the engineer was utilized to minimize the risk of issues arising from improperly soldered or damaged components.

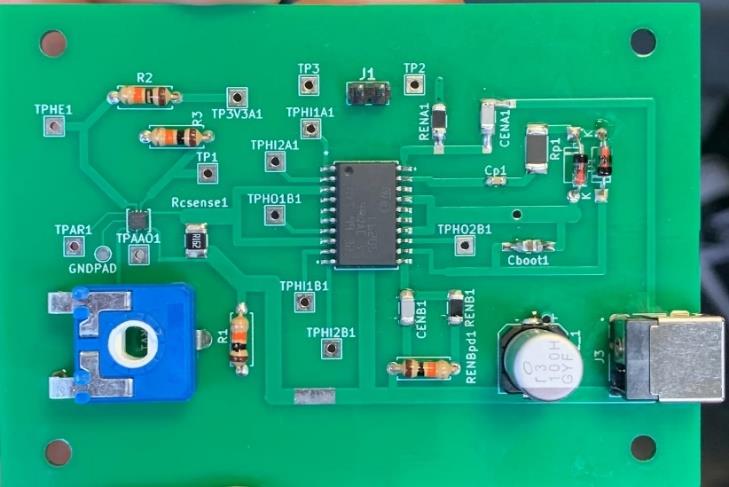
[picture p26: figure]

Figure 1. Soldered printed circuit board.

- The Mechanical Actuation assembly is designed to interface directly with the DUT, positioning the actuator over the buttons to be tested. This component includes a clamp that securely attaches to the DUT, providing flexibility and adaptability for different button placements and device sizes. Mounted within the clamp is a linear actuator that performs the physical pressing of the buttons, with a force sensor placed behind the actuator to capture the exact force applied during each press. This assembly connects to a

PCB board, which relays signals from the force sensor back to the Control Unit, ensuring accurate control and data capture throughout the testing process.

Figure 2 and Figure 3 show the mechanical part isolated and applied to the test device, respectively.

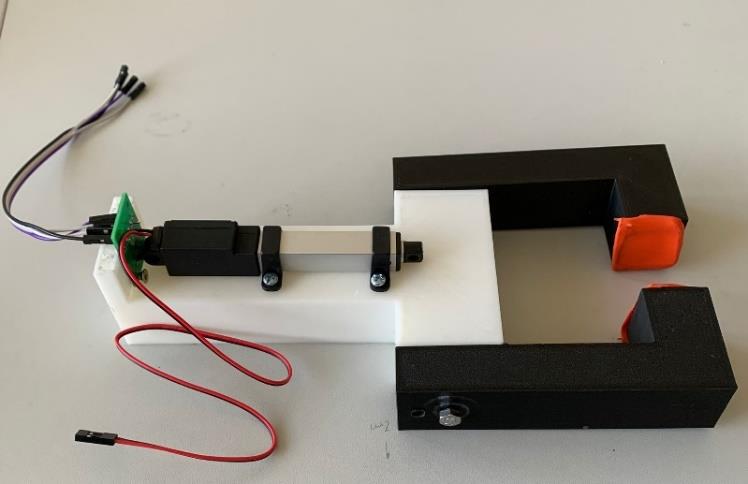
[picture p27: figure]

Figure 2. 3D printed mechanical clamp with embedded actuator and force sensor.

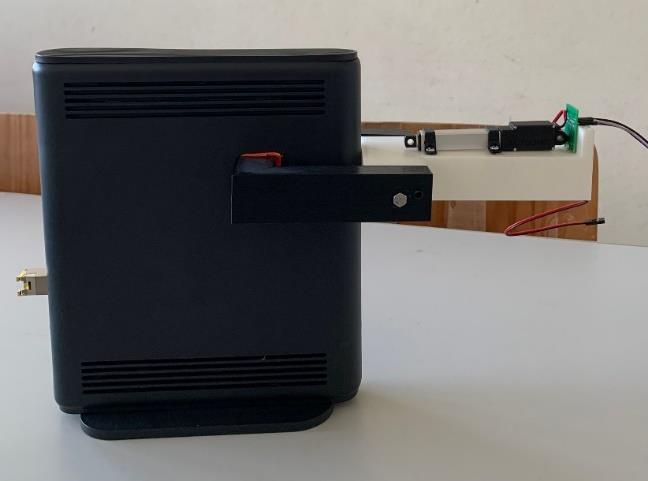
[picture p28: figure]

Figure 3. Mechanical coupler mounted on the test device.

Figure 4 shows the Unified Modelling Language (UML) Sequence Diagram, which represents the interaction amongst the different components of the system.


Figure 4. UML Diagram.

Further details on the system’s architecture can be found in the attached document “BlockDiagrams”.

## Key milestones

ID | Description | Original planned completion date | Current planned completion date | Actual completion date
Communication with Raspberry Pi | Generate test signals and process feedback signals from the DUT. | 04/12/2024 | --/--/-- | 27/11/2024
Design of the mechanical attachment | Development of the mechanical couple using 3D print. | 04/12/2024 | --/--/-- | 5/12/2024

Individual tests
to the main
components

Functionality tests for the main components of the project: force sensor and linear
actuator.
04/12/2024 | --/--/-- | 28/11/2024
Integration of the actuator and sensor into the mechanical design | Mount the linear actuator with force sensor placed immediately behind it on the 3D-printed mechanical clamp | 18/12/2024 | 18/12/2024 | 18/12/2024
Testing basic actuator control using the Raspberry Pi | Test the actuator's response and excursion against the code built in Python. | 18/12/2024 | 18/12/2024 | 18/12/2024

## Progress and deviation from plan

The only hitch we encountered after soldering the printed circuit board was that the team had soldered a connector with a diameter of 2.5mm for the 12V, 3A voltage source, which was incompatible with it. To make up for this, it was simply necessary to unsolder the wrong connector and solder the correct connector with a diameter of 2.1mm.

## Work plan for next iteration

In the next iteration of the project, significant improvements will be made in various areas to improve the system's performance and functionality. In the Web Interface, the focus will be on organizing graphics and information, ensuring a clear presentation of statistics and test history, making it easier for users to analyse the data. In the mechanical coupling, we will work to integrate all the physical parts in a more cohesive way, resulting in a more elegant and discreet structure, suited to the aesthetic and functional requirements of the project. Regarding the DUT's feedback information, a more detailed system will be implemented that includes data such as the number of button presses during tests, offering greater visibility into the behaviour of the device in use. The current limiter will also be optimized with improvements in the sensitivity and robustness of the circuit, ensuring reliable operation even in demanding conditions. These advances aim to strengthen the overall quality of the project, making it more efficient and user-friendly. Finally, the auxiliary accessory for the reset buttons will also be developed.

Figure 5 shows the latest version of the 3D piece that the team intends to develop. In order to balance the force and inertia exerted by the actuator when pressing a button, which caused the weight to tip downwards and become misaligned, it was thought to immerse the actuator in the mechanical part and not leave it on its surface, so that the force is exerted at the centre point of the overall part. Figure 6 shows the updated sprint plan.

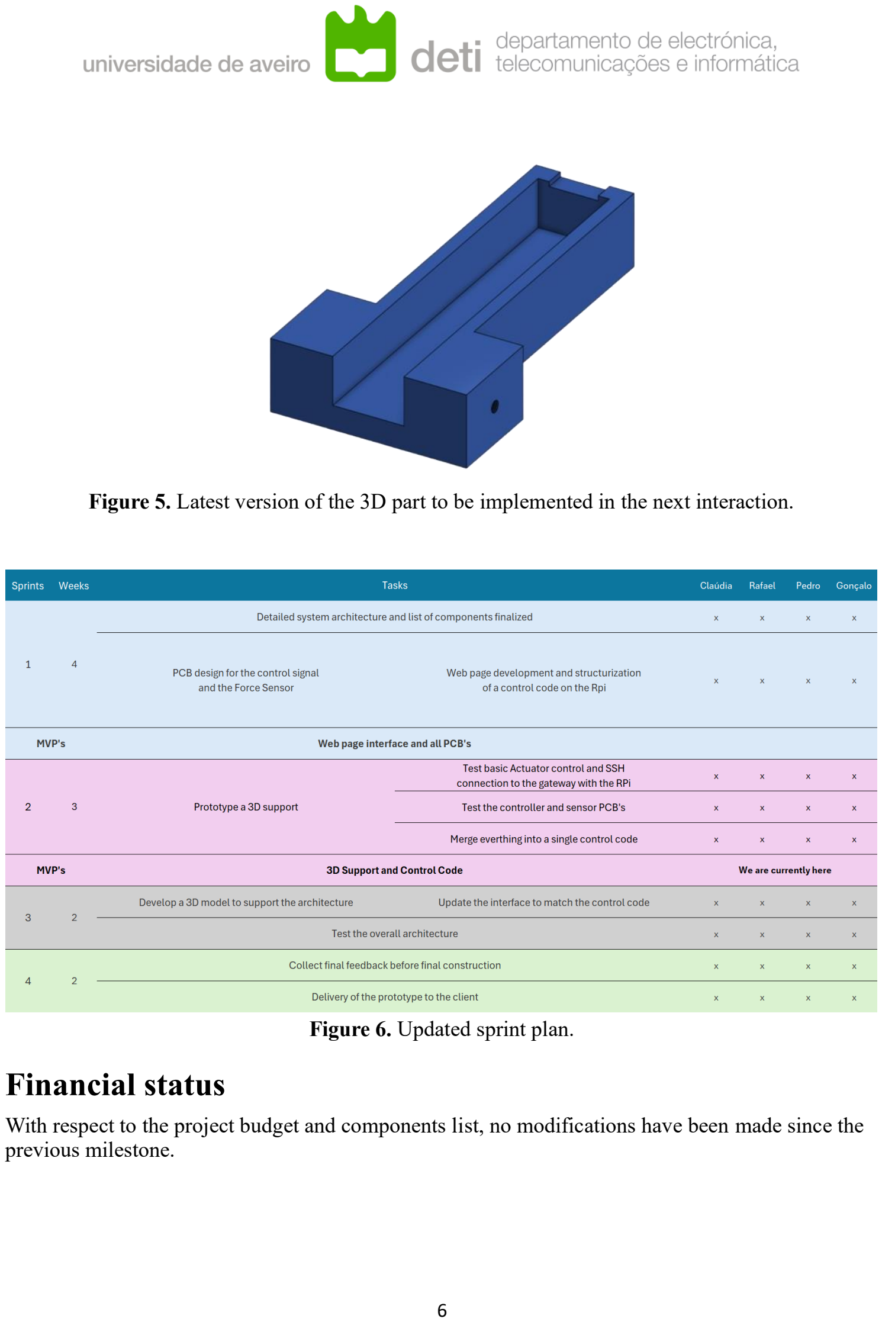
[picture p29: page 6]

Figure 5. Latest version of the 3D part to be implemented in the next interaction.

Figure 6. Updated sprint plan.

## Financial status

With respect to the project budget and components list, no modifications have been made since the previous milestone.

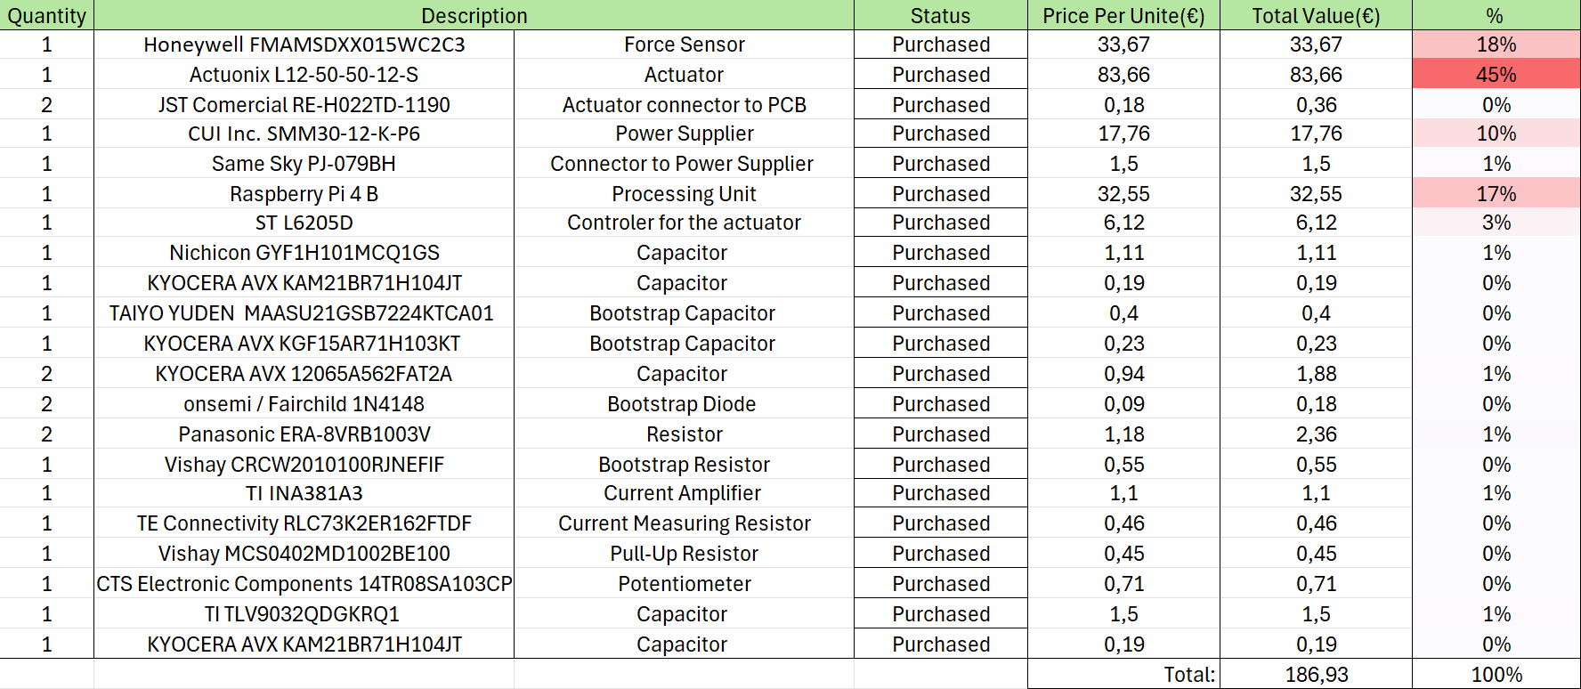
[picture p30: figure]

Figure 7. Updated project budget and final components table.

## Group contribution

Group member | Major contributions | Work share (%)

Cláudia Almeida

Team coordinator, responsible for organizing regrouping sessions and managing communication with external parties. Primary editor of written documents, developed the use cases, studied market relevance for industrial automation. Led Milestone 1 and Milestone 3 presentation. Web interface Development. 3D design and printing. Testing basic actuator control using the Raspberry Pi.

25

Rafael Alves

Developed the final hardware components list, analysed project risks for each phase and proposed mitigation strategies. Led Milestone 1 and Milestone 3 presentation. Development of the PCB. 3D design and printing. Testing basic actuator control using the Raspberry Pi.

25

Gonçalo Peralta

Created all system diagrams and drafts of the mechanical product for documentation, developed the block diagrams and use cases, sprints spread calendar and led the initial planning for the software approach to the project. Web interface Development. Led Milestone presentation 3. Communication with Raspberry Pi. Individual

25

| tests to the main components and testing basic actuator control using the Raspberry Pi.
Pedro Matias | Contributed to researching and finalizing the hardware components list and supported the assessment of technical needs for project phases. Development of the PCB. Individual tests to the main components and testing basic actuator control using the Raspberry Pi. | 25

## Lessons Learned

Throughout the development of this project, several valuable lessons were learned, contributing to the improvement of processes and the success of the team. One of the main lessons was the importance of parallelism between tasks, which allowed different aspects of the project to be worked on simultaneously, speeding up progress without compromising quality. To support this approach, we adopted a dynamic division of teams, which proved essential for quickly adapting human resources to the needs of each project phase, guaranteeing efficiency and flexibility.

The implementation of short daily stand-up meetings, lasting between 5 and 10 minutes, was also a crucial element. These meetings fostered communication between team members, ensuring continuous alignment and rapid problem identification and resolution. Another lesson learned was adaptability in the face of unforeseen events. As unexpected challenges arose, it became clear that the ability to recalibrate plans and priorities in real time and to not go into a state of panic is indispensable for the success of complex projects.

In addition, we learned the importance of a good understanding of the project's objective right from the start, with regular alignments between the team and the advisors. These moments of harmony ensured that everyone involved had a clear and unified vision, reducing ambiguity and rework. Finally, the importance of detailed and coherent documentation became clear. It served as a reliable reference guide, facilitating both the monitoring of progress and the continuation of work at later stages. These lessons, as well as optimizing the execution of the project, will be fundamental pillars in future projects.

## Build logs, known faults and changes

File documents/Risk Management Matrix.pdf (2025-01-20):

# | Risk | Consequence | Likelihood | Severity | Level | Solution | Consequence | R_Likel. | R_Sever. | R_Level

1 | Linear actuator pushing buttons too hard | Damage the equipment | Remote | Critical | 2

Defining a fixed maximum value of pressure, by limiting the output of the amplifier

Limiting the pressure may cause the Actuator
not being able to push the button | Unlikely | Marginal | 4
2 | Poor placement of the automaton on the DUT | Create a misalignment between the actuator and the buttons, resulting in a situation where the buttons aren´t pressed | Occasional | Marginal | 3 | Use a flexible clamp to ease the placement according to the button position | Does not guarantee that the clamp is well placed, it just allows easier adjustments and still needs for the user to test the placement | Remote | Negligible | 4
3 | Improper placement of the force sensor | The applied force may not be measured correctly | Unlikely | Critical | 3 | Ensure the FSR placement gives an accurate measurement on the given test devices by testing different locations for its application | We may need more than one sensor, to compare the values between them and to perform tests simultaneously, incresing the costs | Remote | Negligible | 4
4 | PCB taking up to two or three weeks to build | Delay in the progress, and the component might not work as expected | Likely | Critical | 1 | Use a perforated circuit board instead which will take just a few days to set up | Necessity to acquire new components and to develop a new type of circuit, increasing the costs of the project and time devoted to its construction | Remote | Marginal | 3
5 | Delay on the delivery of the components | Slows the overall progress of the project | Likely | Critical | 1 | Approach the problem with temporary equipment | The usage of diferent components may result in different results than the ones expected, resulting in the definition of innapropriate reference values | Remote | Marginal | 3
6 | Poor team and time management | Lead to task accumulation | Remote | Critical | 2 | Follow the Scrum methodology | -------- | Unlikely | Marginal | 4
7 | Damage the delivered components | Purchase new components and slow the overall project | Remote | Critical | 2 | Purchase more than one component at the start and establish a set of utilization standarts to protect the equipment | Higher cost | Remote | Marginal | 3
8 | The Raspberry Pi may not be fast enought to handle our software | Delays on the WebPage and the control code | Remote | Critical | 2 | Use a faster programing language | Rebuild the software from start | Occasional | Marginal | 3
Unlikely | Negligible | 4 | Unlikely | Negligible | 4
Remote | Marginal | 3 | Remote | Marginal | 3
Likely | Marginal | 2 | Likely | Marginal | 2
Frequent | Catastrophic | 1 | Frequent | Catastrophic | 1
Initial analysis | Residual risk analysis

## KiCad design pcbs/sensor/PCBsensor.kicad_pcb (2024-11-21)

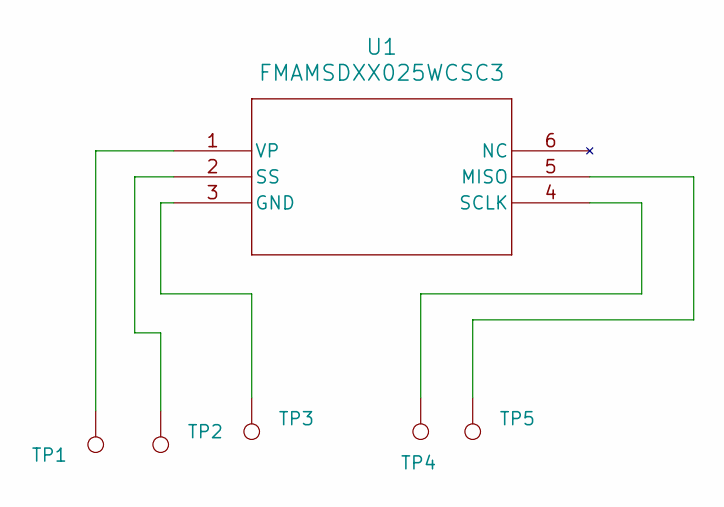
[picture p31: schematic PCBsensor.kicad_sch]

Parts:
TP1, TP2, TP3, TP4, TP5: TestPoint; TestPoint_THTPad_2.0x2.0mm_Drill1.0mm
U1: FMAMSDXX025WCSC3; FMAMSDXX025WCSC3_HNW

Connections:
unnamed: TP3.1, U1.3 (GND)
unnamed: TP5.1, U1.5 (MISO)
unnamed: TP4.1, U1.4 (SCLK)
unnamed: TP2.1, U1.2 (SS)
unnamed: TP1.1, U1.1 (VP)

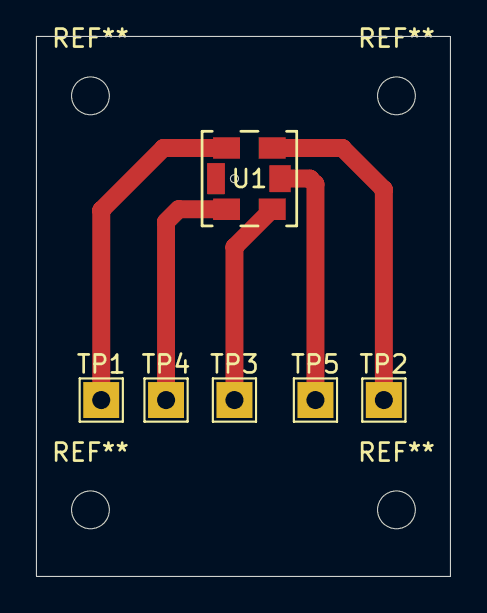
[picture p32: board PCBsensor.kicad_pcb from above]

Board: 2 copper layers, 23.0 x 30.0 mm, 6 parts (0 on the bottom side), 5 nets.

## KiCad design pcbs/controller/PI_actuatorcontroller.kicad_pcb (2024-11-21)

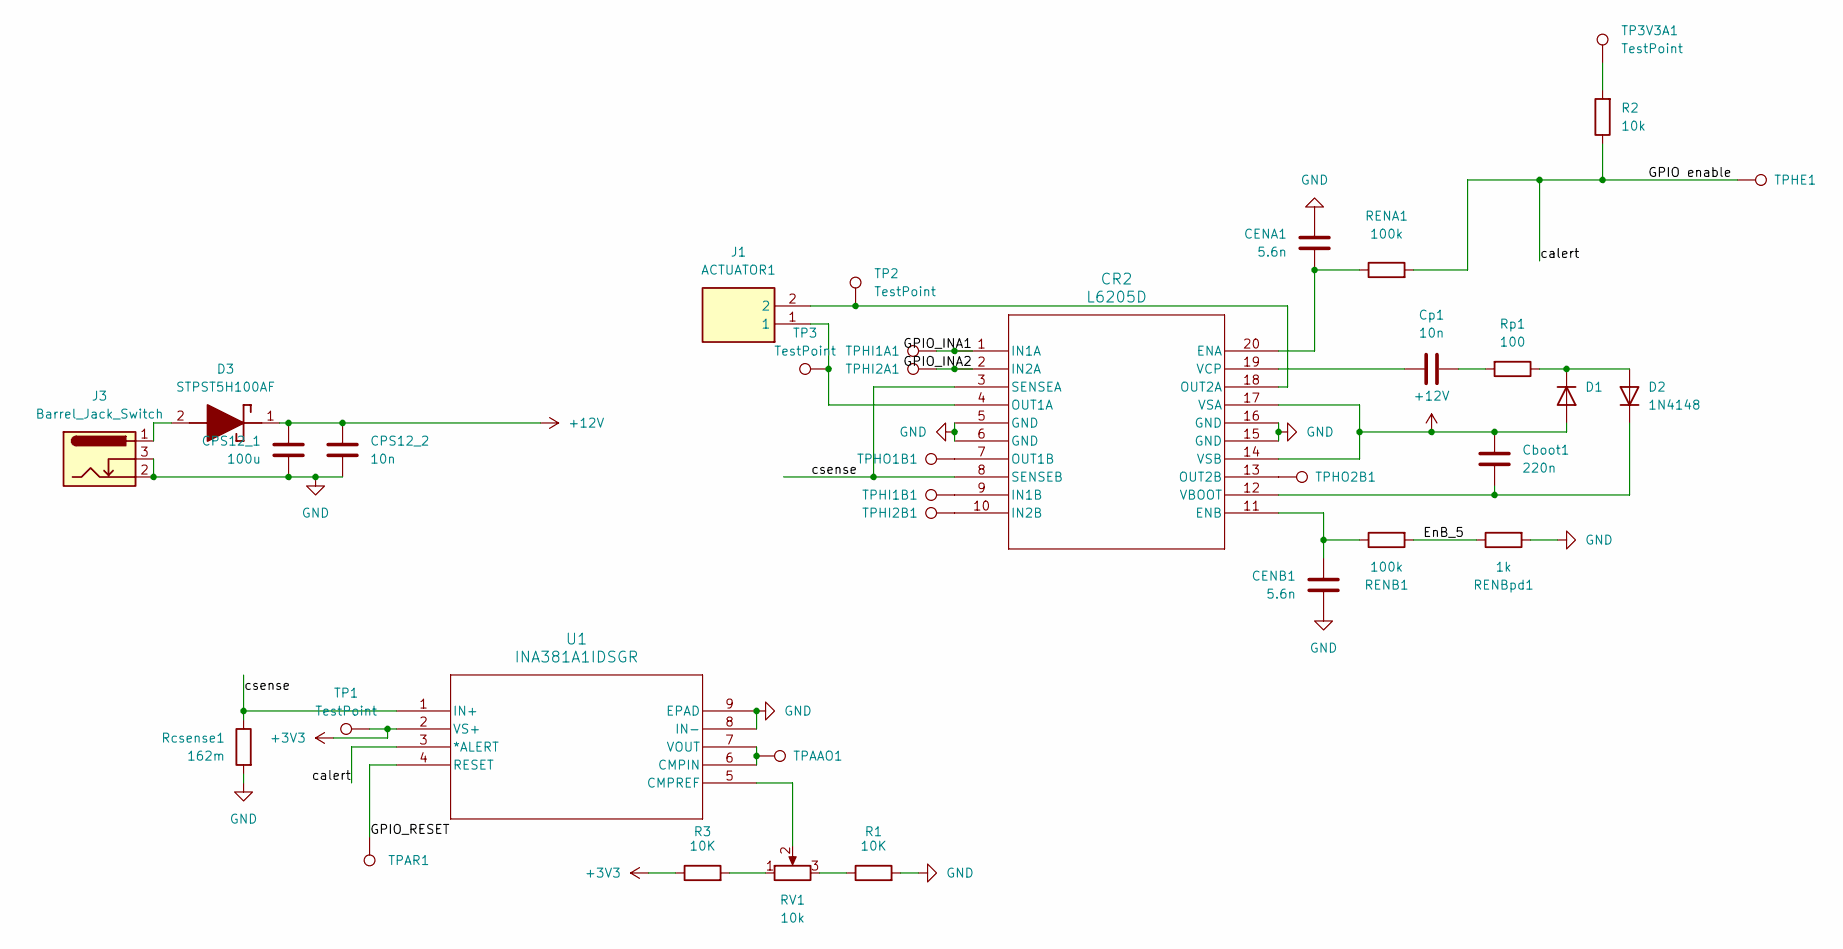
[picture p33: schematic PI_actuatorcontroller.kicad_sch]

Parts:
CENA1: 5.6n; C_1206_3216Metric_Pad1.33x1.80mm_HandSolder
CENB1: 5.6n; C_1206_3216Metric_Pad1.33x1.80mm_HandSolder
CPS12_1: 100u; CP_Elec_8x10
CPS12_2: 10n; C_1206_3216Metric_Pad1.33x1.80mm_HandSolder
CR2: L6205D; SO-20_STM
Cboot1: 220n; C_0805_2012Metric_Pad1.18x1.45mm_HandSolder
Cp1: 10n; C_0603_1608Metric_Pad1.08x0.95mm_HandSolder
D1, D2: 1N4148; D_DO-35_SOD27_P7.62mm_Horizontal
D3: STPST5H100AF; SODFL4724X103N; Manufacturer_Part_Number STPST5H100AF
J1: ACTUATOR1; REH022TD1190LFSN; Manufacturer_Part_Number RE-H022TD-1190(LF)(SN)
J3: Barrel_Jack_Switch; CUI_PJ-079BH
R1, R3: 10K; R_Axial_DIN0207_L6.3mm_D2.5mm_P7.62mm_Horizontal
R2: 10k; R_Axial_DIN0207_L6.3mm_D2.5mm_P7.62mm_Horizontal
RENA1: 100k; R_1206_3216Metric_Pad1.30x1.75mm_HandSolder
RENB1: 100k; R_1206_3216Metric_Pad1.30x1.75mm_HandSolder
RENBpd1: 1k; R_Axial_DIN0207_L6.3mm_D2.5mm_P7.62mm_Horizontal
RV1: 10k; CTSpot
Rcsense1: 162m; R_1210_3225Metric_Pad1.30x2.65mm_HandSolder
Rp1: 100; R_2010_5025Metric_Pad1.40x2.65mm_HandSolder
TP1, TP2, TP3, TP3V3A1: TestPoint; TestPoint_THTPad_2.0x2.0mm_Drill1.0mm
TPAAO1: TestPoint; TestPoint_THTPad_2.0x2.0mm_Drill1.0mm
TPAR1: TestPoint; TestPoint_THTPad_2.0x2.0mm_Drill1.0mm
TPHE1: TestPoint; TestPoint_THTPad_2.0x2.0mm_Drill1.0mm
TPHI1A1, TPHI1B1, TPHI2A1, TPHI2B1: TestPoint; TestPoint_THTPad_2.0x2.0mm_Drill1.0mm
TPHO1B1, TPHO2B1: TestPoint; TestPoint_THTPad_2.0x2.0mm_Drill1.0mm
U1: INA381A1IDSGR; DSG_8_TEX

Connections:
+3V3: R3.1, TP1.1, U1.2 (VS+)
+12V: CPS12_1.1, CPS12_2.1, CR2.14 (VSB), CR2.17 (VSA), Cboot1.1, D1.2 (A), D3.1 (K)
/EnB_5: RENB1.2, RENBpd1.1
/GPIO enable: R2.1, RENA1.2, TPHE1.1, U1.3 (*ALERT)
/GPIO_INA1: CR2.1 (IN1A), TPHI1A1.1
/GPIO_INA2: CR2.2 (IN2A), TPHI2A1.1
/GPIO_RESET: TPAR1.1, U1.4 (RESET)
/csense: CR2.3 (SENSEA), CR2.8 (SENSEB), Rcsense1.1, U1.1 (IN+)
GND: CENA1.1, CENB1.2, CPS12_1.2, CPS12_2.2, CR2.5 (GND), CR2.6 (GND), CR2.15 (GND), CR2.16 (GND), J3.2, J3.3, R1.2, RENBpd1.2, Rcsense1.2, U1.8 (IN-), U1.9 (EPAD); also elsewhere on the board
unnamed: CENA1.2, CR2.20 (ENA), RENA1.1
unnamed: CENB1.1, CR2.11 (ENB), RENB1.1
unnamed: CR2.9 (IN1B), TPHI1B1.1
unnamed: CR2.10 (IN2B), TPHI2B1.1
unnamed: CR2.4 (OUT1A), J1.1, TP3.1
unnamed: CR2.7 (OUT1B), TPHO1B1.1
unnamed: CR2.18 (OUT2A), J1.2, TP2.1
unnamed: CR2.13 (OUT2B), TPHO2B1.1
unnamed: CR2.12 (VBOOT), Cboot1.2, D2.1 (K)
unnamed: CR2.19 (VCP), Cp1.1
unnamed: Cp1.2, Rp1.2
unnamed: D1.1 (K), D2.2 (A), Rp1.1
unnamed: D3.2 (A), J3.1
unnamed: R1.1, RV1.3
unnamed: R2.2, TP3V3A1.1
unnamed: R3.2, RV1.1
unnamed: TPAAO1.1, U1.6 (CMPIN), U1.7 (VOUT)
unnamed: RV1.2, U1.5 (CMPREF)

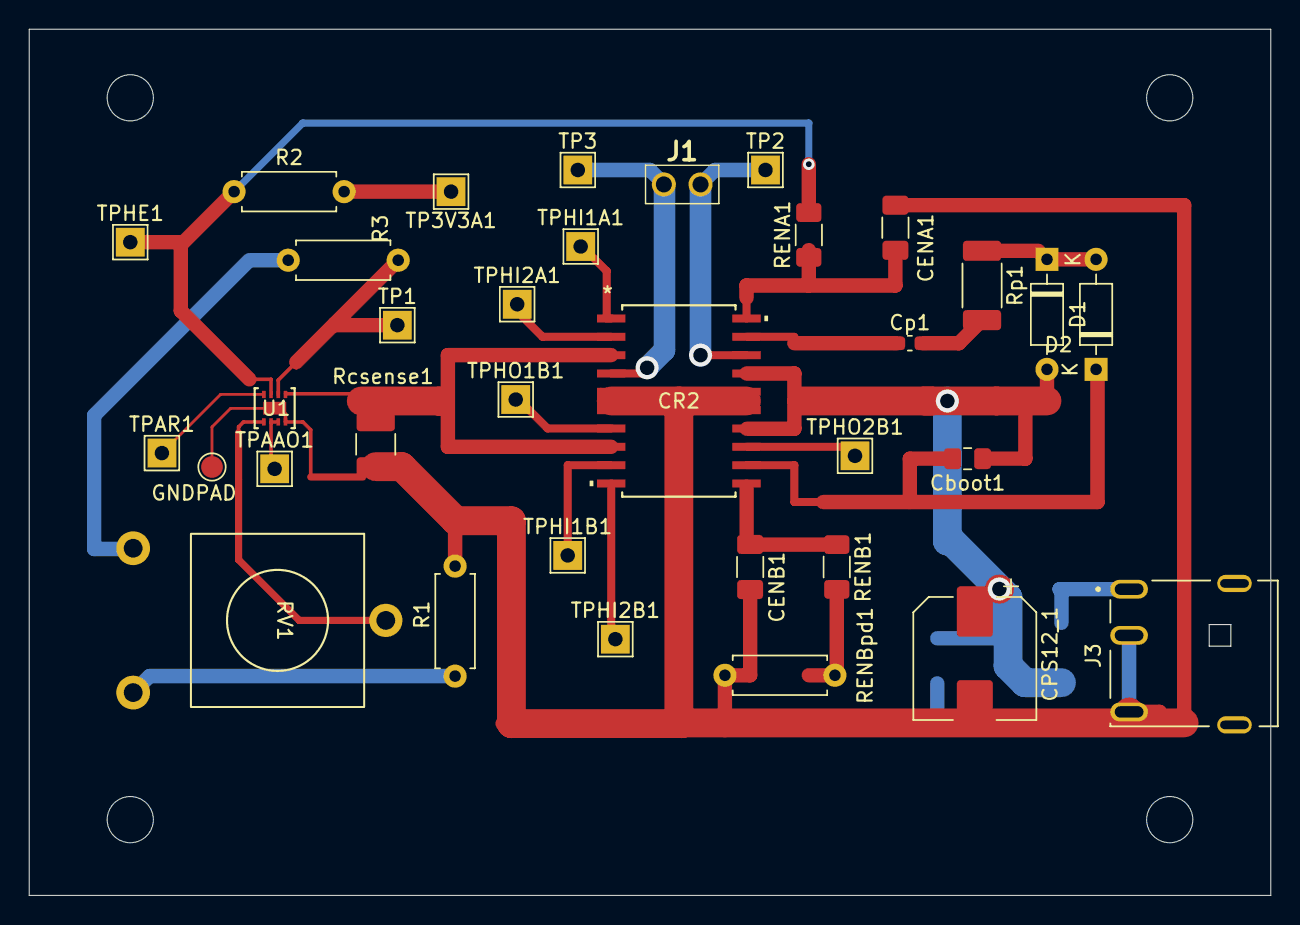
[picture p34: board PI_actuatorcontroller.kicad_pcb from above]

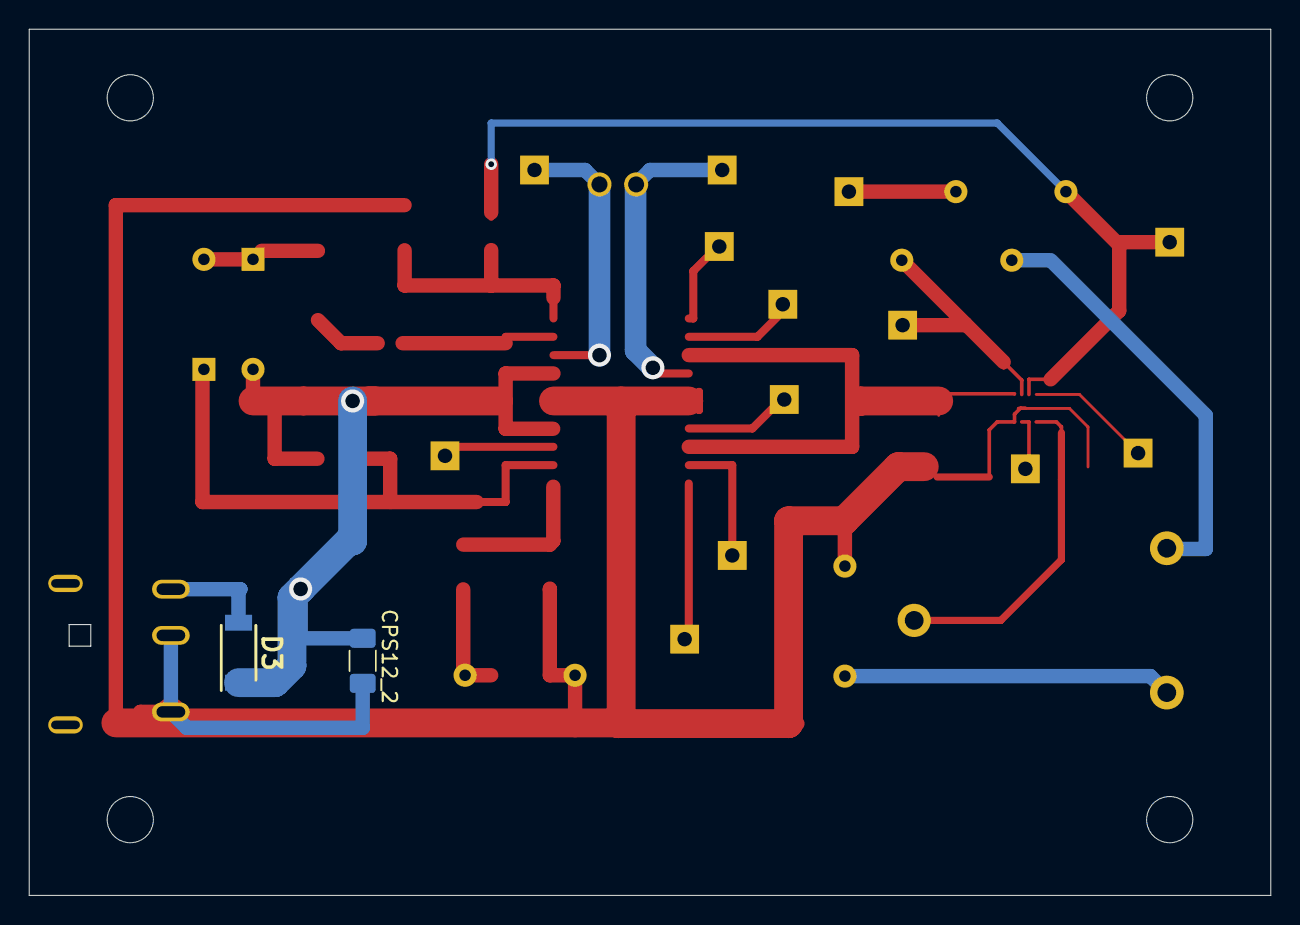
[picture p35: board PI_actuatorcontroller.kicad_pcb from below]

Board: 2 copper layers, 86.0 x 60.0 mm, 36 parts (2 on the bottom side), 27 nets.

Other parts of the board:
GNDPAD: TestPoint_Pad_D1.5mm

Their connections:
GND: GNDPAD.1; also elsewhere on the board

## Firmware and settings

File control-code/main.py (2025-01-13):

import uvicorn
import logging
import threading
from api import app
from state import State
from ssh import SSHConnect
from sensor_reader import SensorReader
from control_signal import ControlCode

def setupLogging():
    logging.basicConfig(filename='app.log', level=logging.INFO, format='%(asctime)s - %(name)s - %(levelname)s - %(message)s')

def StartAPI():
    uvicorn.run(app, host='0.0.0.0', port=8000, timeout_keep_alive=10000)

def main():
    setupLogging()

    APIth = threading.Thread(target=StartAPI)
    STATEth = threading.Thread(target=State)
    SSHth = threading.Thread(target=SSHConnect)
    CONTROLth = threading.Thread(target=ControlCode)
    SENSORth = threading.Thread(target=SensorReader)
    
    APIth.start()
    STATEth.start()
    SSHth.start()
    CONTROLth.start()
    SENSORth.start()

    APIth.join()
    STATEth.join()
    SSHth.join()
    CONTROLth.join()
    SENSORth.join()

if __name__ == '__main__':
    main()

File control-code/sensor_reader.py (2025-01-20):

import logging
import threading
from smbus2 import SMBus # type: ignore
from numpy import linspace
import shared_memory as sh
from time import (sleep, perf_counter)

logger = logging.getLogger("SENSOR")

OutputMAX = 0.8 * 2**14
OutputMIN = 0.2 * 2**14
ForceRated = 15
Force = 0

def SensorReader():
    while True:
        # Sensor Loop
        # 1 - Wait for start
        # 2 - Get the pressTime parameter
        # 3 - Store current time
        # 4 - Read force values
        # 5 - If force is greater than a threshold read for the pressTime and 2 more seconds
        # 6 - Store the results on the shared dictionary
        # 7 - Resume the state module
        # Repeat
        
        sh.startSensorAndControl.acquire()      # Wait for the SSH connection
        logger.info("Sensor module started")

        flag = 0
        with sh.access:
            holdTime = sh.parameters.pressTime
            sh.modulesData['force_val'] = []
            sh.modulesData['time_val'] = []

        print("\033[95m[SENSOR] Starting to read from force sensor\033[00m")
        logger.info("Starting to read from force sensor")

        tic = perf_counter()    # Start counting time
        tic2 = perf_counter()

        with SMBus(1) as bus:
            while True:
                try:
                    bytes = bus.read_i2c_block_data(0x28, 0, 2)
                except OSError:
                    with sh.access:
                        sh.ERROR = 'SENSOR'
                    bytes = [1, 1]
                Output = (bytes[0] << 8) + bytes[1];
                Force = (Output-OutputMIN)*ForceRated/(OutputMAX-OutputMIN)
                if Force < 0:   # Sensor gives -0.15 as the lowest value
                    Force = 0

                with sh.access:
                    sh.modulesData['force_val'].append(round(Force, 4))

                if flag == 0:
                    if Force > 5: # If more than 5 newtons are read stop the actuator
                        logger.info("Sensed force greater than 5 Newtons")
                        with sh.access:
                            sh.PRESSED = True
                        flag = 1
                        tic2 = perf_counter()
                        print(tic2)
                        sh.buttonPressed.release(2)
                    
                    if (perf_counter() - tic) > 5:  # Timeout 5 sec
                        logger.info("Timed out")
                        sh.buttonPressed.release(2)
                        break

                elif perf_counter() > (tic2 + holdTime + 1):
                    print(f"{perf_counter()} -> {tic2+holdTime+2}")
                    logger.info("Stoped reading")
                    break
                sleep(0.01)
        
        if flag:
            time = linspace(0, perf_counter()-tic, len(sh.modulesData['force_val'])).tolist()
            sh.modulesData['time_val'] = [round(el, 3) for el in time]

        print("\033[95m[SENSOR] Readings ready\033[00m")
        logging.info("Force readings ready")
        sh.sensorReadingsReady.release()

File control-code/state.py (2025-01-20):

import logging
import sqlite3 as sql
from time import sleep
from smbus2 import SMBus # type: ignore
import shared_memory as sh
from datetime import datetime

logger = logging.getLogger("STATE")

def testI2C():
    with SMBus(1) as bus:
        try:
            bus.read_i2c_block_data(0x28, 0, 2)
        except OSError:
            with sh.access:
                sh.ERROR = "Couldn't connect to the force sensor"
                sh.feedback = {
                    'button': 'No feedback',
                    'success': 0
                }
                sh.readings['val'] = [0, 0, 0] 
                sh.readings['time'] = [0, 0, 0]
                sh.feedbackReady.release()
                sh.sensorReadingsReady.release()
    
def State():
    while True:
        # State Loop
        # 1 - Wait for start
        # 2 - Get parameters of the test
        # 3 - Start the SSH module
        # 4 - Wait until Sensor and SSH finish
        # 5 - Store the modules data
        # 6 - Wait the interval between actuations
        # 7 - Repeat for nTimes
        # 8 - Store data on the database
        # Repeat

        sh.startTest.acquire()
        logger.info("Starting a test")

        rowID = 0
        
        with sh.access:
            sh.resetModulesData()
            n = sh.parameters.nTimes
            wait = sh.parameters.interval
            sh.STATE = sh.state.RUNNING
            sh.CURRENT_RUN = 0
            sh.ERROR = 'No Error'

            db = sql.connect("app.db")
            cur = db.cursor()
            
            rowID = cur.execute(f"INSERT INTO tests (success, parameters, force_val, time_val) VALUES (\"[\", \"{[sh.parameters.pressTime, sh.parameters.nTimes, sh.parameters.interval]}\", \"[\", \"[\")").lastrowid
            
            db.commit()
            cur.close()
            db.close()
        

        testI2C()
        
        for i in range(n):
            with sh.access:
                if sh.ERROR != 'No Error':
                    break
            # Start SSH Module
            sh.startSSH.release()
            logger.info(f"Starting actuation: {i+1}/{n}")

            # Wait until the other modules finish...
            sh.sensorReadingsReady.acquire()
            sh.feedbackReady.acquire()
            logger.info("Storing test data on database")

            # Store data on variable
            with sh.access:
                db = sql.connect("app.db")
                cur = db.cursor()
        
                if i == 0:
                    cur.execute(f"UPDATE tests SET success = success || \"{sh.modulesData['success']}\", force_val = force_val || \"{sh.modulesData['force_val']}\", time_val = time_val || \"{sh.modulesData['time_val']}\" WHERE id = {rowID}")
                else:
                    cur.execute(f"UPDATE tests SET success = success || \", {sh.modulesData['success']}\", force_val = force_val || \", {sh.modulesData['force_val']}\", time_val = time_val || \", {sh.modulesData['time_val']}\" WHERE id = {rowID}")
                
                db.commit()
                cur.close()
                db.close()

            if i != n-1:
                logger.info(f"Waiting interval between actuations: {wait}s")
                sleep(wait)

            with sh.access:
                sh.CURRENT_RUN = sh.CURRENT_RUN + 1
                if sh.STATE == sh.state.ABORT:
                    logger.warning("Aborting current test")
                    sh.STATE = sh.state.READY
                    break
    
        
        logger.info("Test finished. Storing last parameters on database")
        # Store data on the database
        now = datetime.now()
        date = now.strftime("%d-%m-%Y")
        time = now.strftime("%H:%M:%S")
        
        with sh.access:
            db = sql.connect("app.db")
            cur = db.cursor()

            cur.execute(f"UPDATE tests SET button = \"{sh.modulesData['button']}\", success = success || \"]\", error = \"{sh.ERROR}\", presses = {sh.CURRENT_RUN}, force_val = force_val || \"]\", time_val = time_val || \"]\", date = \"{date}\", time = \"{time}\" WHERE id = {rowID}")

            db.commit()
            cur.close()
            db.close()

        with sh.access:
            sh.STATE = sh.state.READY
            sh.CURRENT_RUN = 1
            sh.parameters.pressTime = 0
            sh.parameters.interval = 0
            sh.parameters.nTimes = 1

        logger.info("Test finished")

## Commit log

2024-11-09 adding graph on start button click to home page
2024-11-11 adding scrolling on start button in home page
2024-11-13 adding filtering to search bar in history page
2024-11-14 Adicionei o botão On na lista de testes pré-definindos
2024-11-18 concurrent program to read values of a sensor (modeled by random integers)
2024-11-18 added PCB files to the repository
    [PI_actuatorcontroller.kicad_pcb, PI_actuatorcontroller.kicad_sch]
2024-11-18 able to send the sensor readings from the control code to the interface and show them
2024-11-19 pcb de terça-feira
    [PI_actuatorcontroller.kicad_pcb, PI_actuatorcontroller.kicad_sch]
2024-11-19 pcbs de terça-feira
    [PCBsensor.kicad_pcb, PCBsensor.kicad_sch, PI_actuatorcontroller.kicad_pcb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]
2024-11-21 PCB controller final version
    [PI_actuatorcontroller.kicad_pcb, PI_actuatorcontroller.kicad_sch]
2024-11-21 PCB sensor final version
    [PCBsensor.kicad_pcb, PCBsensor.kicad_sch]
2024-11-21 reading button pushes from ssh
2024-11-23 fixed and cleaned some minor issues
    [main.py, sensor_reader.py, ssh.py]
2024-11-23 Able to get button feedback on the SSH connection
2024-11-26 reworking database, history and statistics
    [api.py, ssh.py]
2024-11-29 updating the ssh code with the new method to get the button feedback, interface is not yet matched
2024-11-30 finishing the profile system on the main page with add and delete buttons
2024-12-02 simple control code to test once the pcb's are done
2024-12-06 fixing history table and minor bugs on home page
    [control_signal.py]
2024-12-08 adding test codes for the sensor and the control circuit
2024-12-11 adding the updated sensor and controller test codes
2024-12-11 fixing minor rooting problems
    [api.py, control_signal.py]
2024-12-12 adding sensor code to interface
2024-12-12 connecting sensor to interface
2024-12-14 working version of the sensor code
2024-12-14 re-commit of the sensor working version
2024-12-23 adding sensor feedback on control code
2024-12-23 reworking folder structure
    [PCBsensor.kicad_pcb, PCBsensor.kicad_sch, PI_actuatorcontroller.kicad_pcb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]
2024-12-29 working on the api module, adding endpoints for the database and fixing history and statistics
    [api.py]
2024-12-29 fixing home page and deleting old api
    [api.py]
2025-01-08 matching interface with control-code and fixing typos
    [main.py]
2025-01-12 making interface responsive for smaller screens, handling some exeptions, deleting trash files and reworking folder structure
    [api.py, control_signal.py, createDatabase.py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]
2025-01-12 handling i2c exceptions
2025-01-13 adding status bar, and improving the data download
    [data.csv]
2025-01-13 working on api reference page, adding download to log file, adding more error handling
    [data.csv]
2025-01-15 adding the 3d design files to the repository
    [PeçaPrincipal.stl, box.stl, grampofinal.stl]
2025-01-17 updating sql queries, fixing the home page graph taking too long to update and removing useless files
    [api.py, control_signal.py, main.py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]
2025-01-20 switching database to default state
